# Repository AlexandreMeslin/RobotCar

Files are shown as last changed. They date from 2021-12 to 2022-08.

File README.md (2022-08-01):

# RobotCar

Lista de material:

- 1 Arduino Uno
- 1 Sensor shield v5.0
- 1 chassis duplo de acrílico para carro com 4 rodas
- 4 motores DC
- 4 rodas
- 1 módulo bluetooth HC-06 (HC-06 bluetooth module)
- 1 ponte dupla H SparkFun L298 (Dual H-Bridge motor drivers L298)
- 1 servo-motor SG90 (SG90 Micro-servo motor)
- 1 sensor de ultrassom (Ultrasonic Sensor HC-SR04)
- 1 placa de sensores versão 5 (Sensor Shield v5)
- 1 alojamento para baterias ou pilhas (3 baterias 18650 ou 4 pilhas alcalinas)

Opcionais:

- 1 Auto-falante piezo-elétrico (piezo speaker ou buzzer)
- 2 LEDs brancos 10 mm
- 2 LEDs vermelhos 5 mm
- 4 resistores 220 ohms

## Errata

Na conexão do motor: o pino 6 deve ser ligado ao ENA e o pino 13 ao IN4. Ambos, ENA e ENB devem ser ligados a saídas PWM.

## Montagem

### Montagem dos motores

Solde os fios vermelhos e pretos nos quatro motores, criando quatro conjuntos iguais. Não existe problema de polaridade, uma vez que o carro irá andar para frente e para trás, ou seja, durante o funcionamento, haverá inversão natural de tensão. Apenas certifique-se de que todos os motores foram montados igualmente.

Use um par de presilhas em cada motor para fixar o motor na parte de cima da placa do chassis inferior. As cabeças dos parafusos devem ficar voltadas para o lado de fora do carro enquanto que as porcas, para o lado de dentro.

Fixe as rodas. Os discos pretos vazados não serão utilizados nesse projeto.

Fixe as rodas com cuidado para não quebrar o acrílico. Certifique-se que as rodas estejam firmemente colocadas.

Uma boa referência para esse montagem está nesse [blog](https://create.arduino.cc/projecthub/andriy-baranov/smartphone-controlled-arduino-4wd-robot-car-14d239).

### Montagem do chassis

O servo-motor vai ser utilizado para direcionar o sensor ultrassom quando o carro andar para frente ou fizer alguma curva da mesma forma que os faróis dos carros topo de linha trabalham. Posicione o servo-motor abaixo do chassis de cima, dentro do furo maior, no lado que você considerar a frente do carro (qualquer ponta pode ser a frente). Marque e fure (dois furos) usando uma broca de aço rápido. Fixe o motor, fixe uma das barras brancas no eixo do servo. Marque e fure (dois furos) o acrílico em L. Fixe usando um parafuso para plástico bem fino. Fixe o sensor ultrassom usando cola quente no acrílico em L.

Posicione o Arduino logo após o sensor em L, depois a ponte, com o discipador de calor voltado para frente, e, na parte mais distante do sensor ultrassom, o alojamento das baterias. Note que dificilmente algum furo vai poder ser aproveitado. Faça as marcações e novos furos para fixar os três elementos. Fixe os três elementos.

Fixe os seis espaçadores separando as duas camadas do chassis.

Após essa etapa, as partes mecânicas devem estar prontas, faltando o cabeamento e o software.

### Cabeamento

Coloque o sensor shield sobre o Arduino.

#### **Cabeamento do sensor ultrassom:**

Alimentação:

- +5V
- GND

I/O:

- GPIO8: TRIGPIN
- GPIO9: ECHOPIN

Para fixar o sensor no suporte acrílico em L foi necessário fazer 4 furos com brocas de 1 mm. Para encaixar o cristal foi necessário limar um pouco o acrílico porque eu utilizei parafusos de óculos e eles eram curtos.

Usando um cabo de quatro fios, conecte o sensor no shield como mostrado a seguir:

| Sensor Ultrassom | Sensor Shield |
| --- | --- |
| Echo | 9 |
| Trig | 8 |
| Vcc | V |
| Gnd | G |

#### **Cabeamento do servo-motor**

Alimentação:

- +5V
- GND

I/O:

- GPIO7: SERVOPIN

O servo-motor é usado para posicionar o sensor ultrassônico sempre na direçao do movimento do carro.

O acrílico deve ser aparafusado em cima do motor usando a barra reta que vem com o motor.

| Servo Motor | Sensor Shield |
| --- | --- |
|  Control  | 7 |
| Vcc | V |
| Gnd | G |

#### **Cabeamento do módulo Bluetooth:**

Alimentação:

- +5V
- GND

I/O:

- TX: TxD
- RX: RxD

Prenda com uma gravatinha (ou um lacre de embalagem de pão) o módulo Bluetooth. Note que ele não tem furação de fixação. Com um cabo de quatro fios, conecte o módulo no shield como mostrado a seguir:

| Módulo Bluetooth | Sensor Shield |
| --- | --- |
| RXD | TX |
| TXD | RX |
| VCC | V |
| GND | G |

#### **Cabeamento da ponte:**

:warning: Ver ERRATA!

Conecte os dois fios vermelhos dos motores direito em OUT4.

Conecte os dois fios pretos dos motores direito em OUT3.

Conecte os dois fios vermelhos dos motores esquerdo em OUT2.

Conecte os dois fios pretos dos motores esquerdo em OUT1.

Termine o cabeamento da ponte como mostrado a seguir (antes, retire os dois jumpers que estão na ponte para fazer o cabeamento):

| Módulo Ponte | Sensor Shield |
| - | - |
| ENA | 5 |
| IN1 | 2 |
| IN2 | 3 |
| IN3 | 4 |
| IN4 | 13 |
| ENB | 6 |

#### **Cabeamento da energia:**

Conecte o fio vermelho da bateria em +12V da ponte.

Conecte o fio preto da bateria em GND da ponte. Nesse mesmo ponto, conecte um fio preto até GND do sensor shield.

Conecte o fio vermelho de VCC da ponte até VCC do shield.

Opcionalmente, conecte o positivo (vermelho) do suporte da bateria no módulo de potência através de uma chave liga-desliga.

#### **Opcionais:**

- LEDs brancos na frente. Dois LEDs brancos, cada um com um resistor de 220 Ω ligados no pino 10
- LEDS vermelhos atrás. Dois LEDs vermelhos, cada um com um resistor de 220 Ω ligados no pino 1
- Buzina: Uma buzina (buzzer) ligada no pino 11
- Chave liga/desliga em série com as baterias.

### Código

:warning: IMPORTANTE: antes de fazer upload do código, não se esqueça de desconectar os pinos TX e RX do shield. Eles estão conectados ao Bluetooth, que usa os mesmos pinos da interface serial USB. Lembre-se de reconectar para poder usar o carro.

## Histórico

- 2022-08-01: Inclusão da câmera frontal no carro.
- 2022-02-17b: Criação de um README (quase) descente.
- 2002-02-17: Primeira versão com controle de versão.

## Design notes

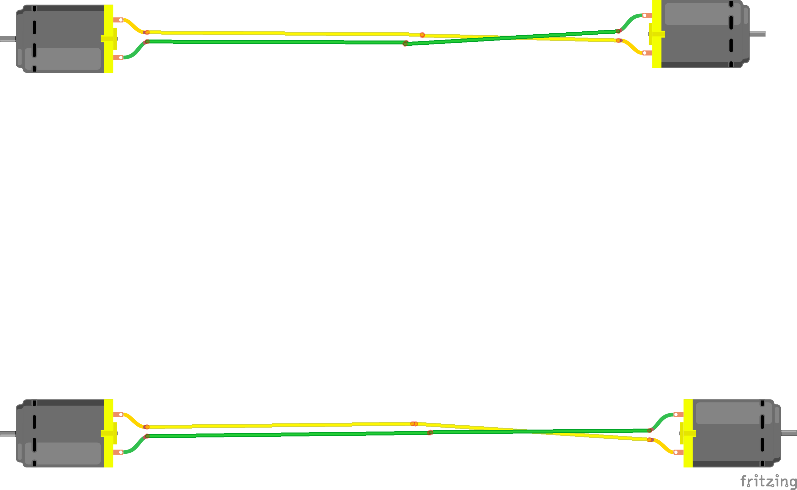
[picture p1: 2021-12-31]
CarroRobo_motores.png

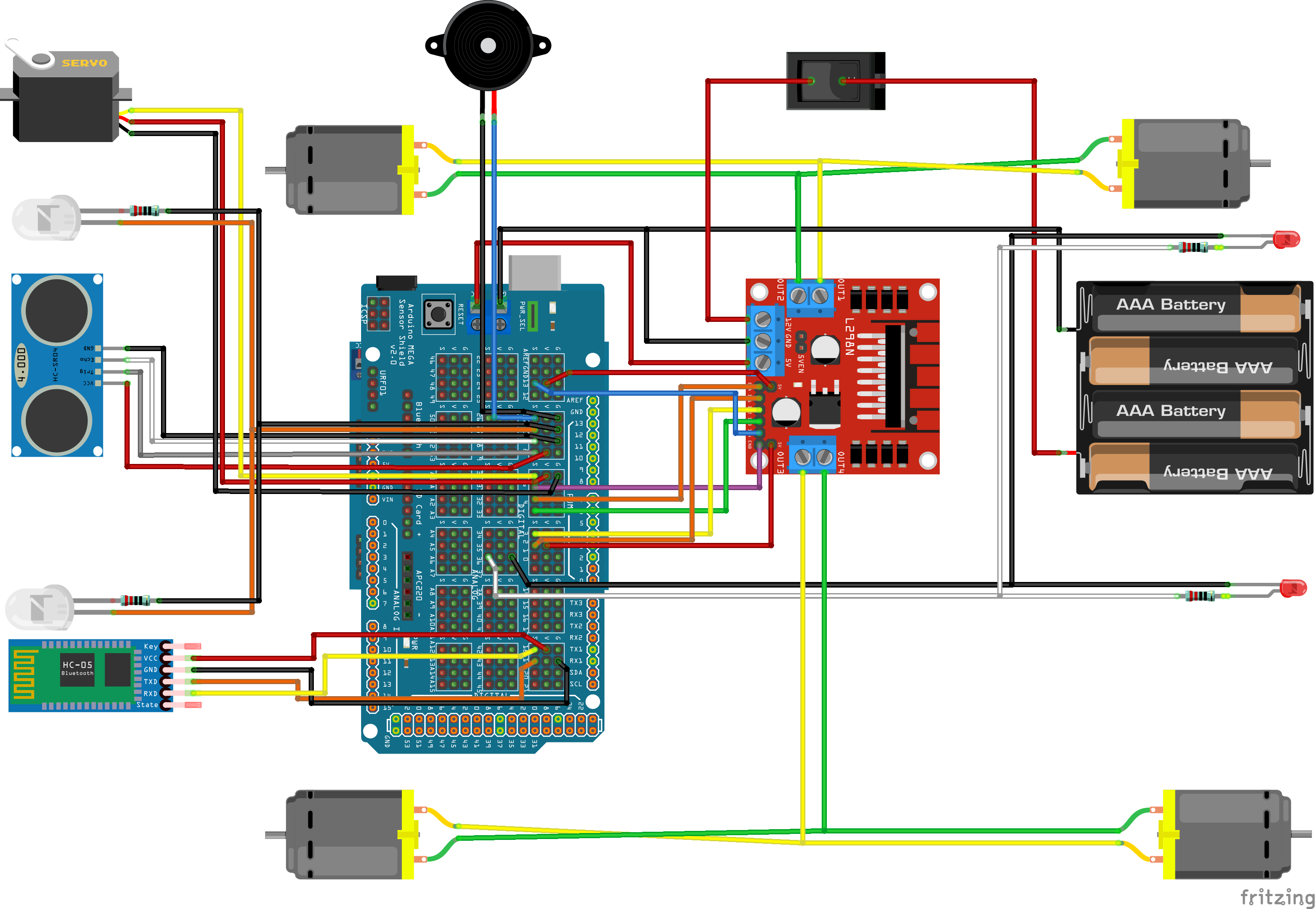
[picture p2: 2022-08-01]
CarroRoboMega_bb.png

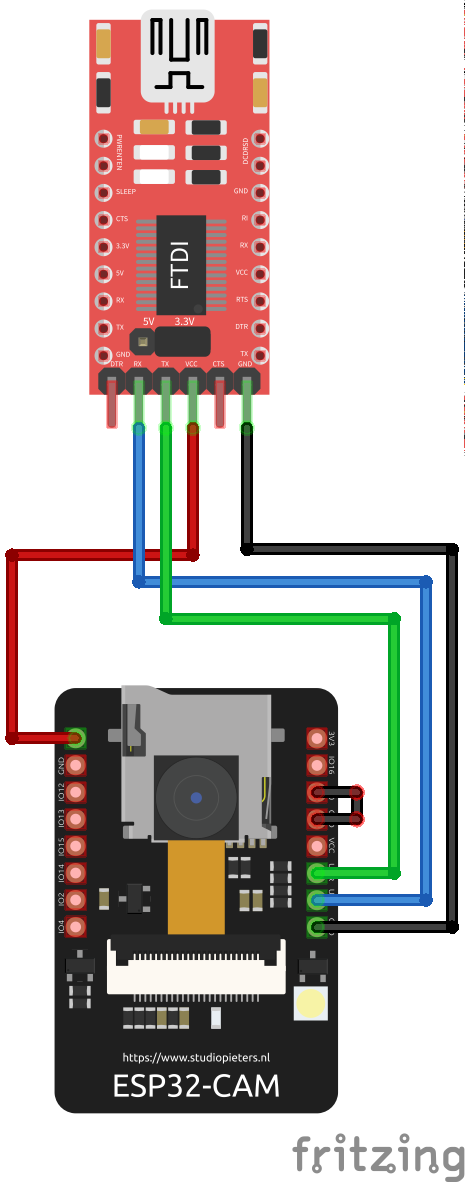
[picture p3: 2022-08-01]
GravacaoESP32Cam_bb.png

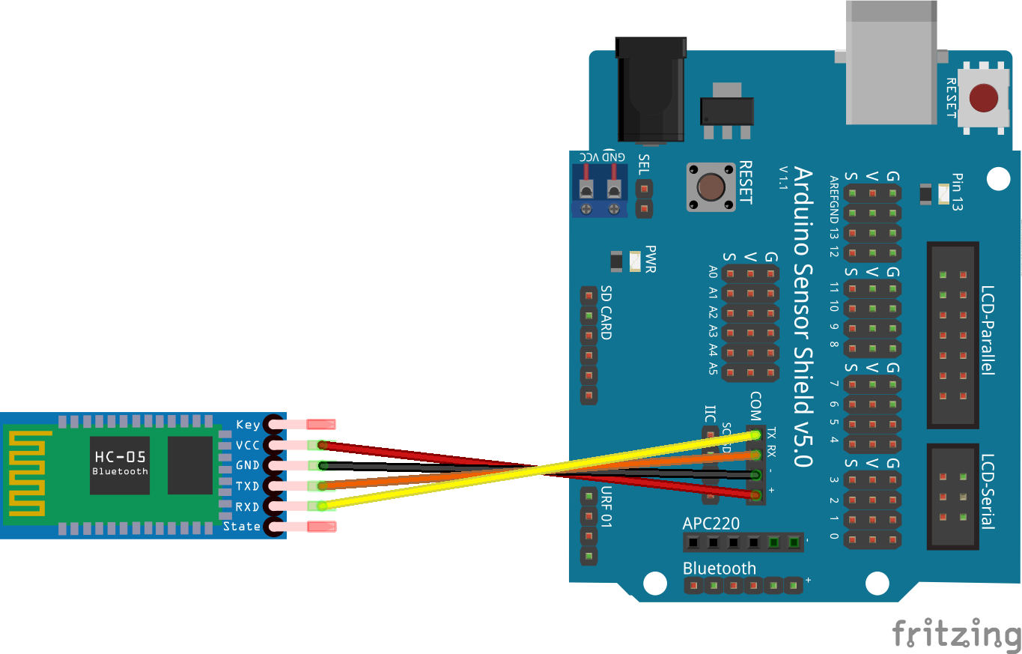
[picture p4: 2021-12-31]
CarroRobo_bluetooth.png

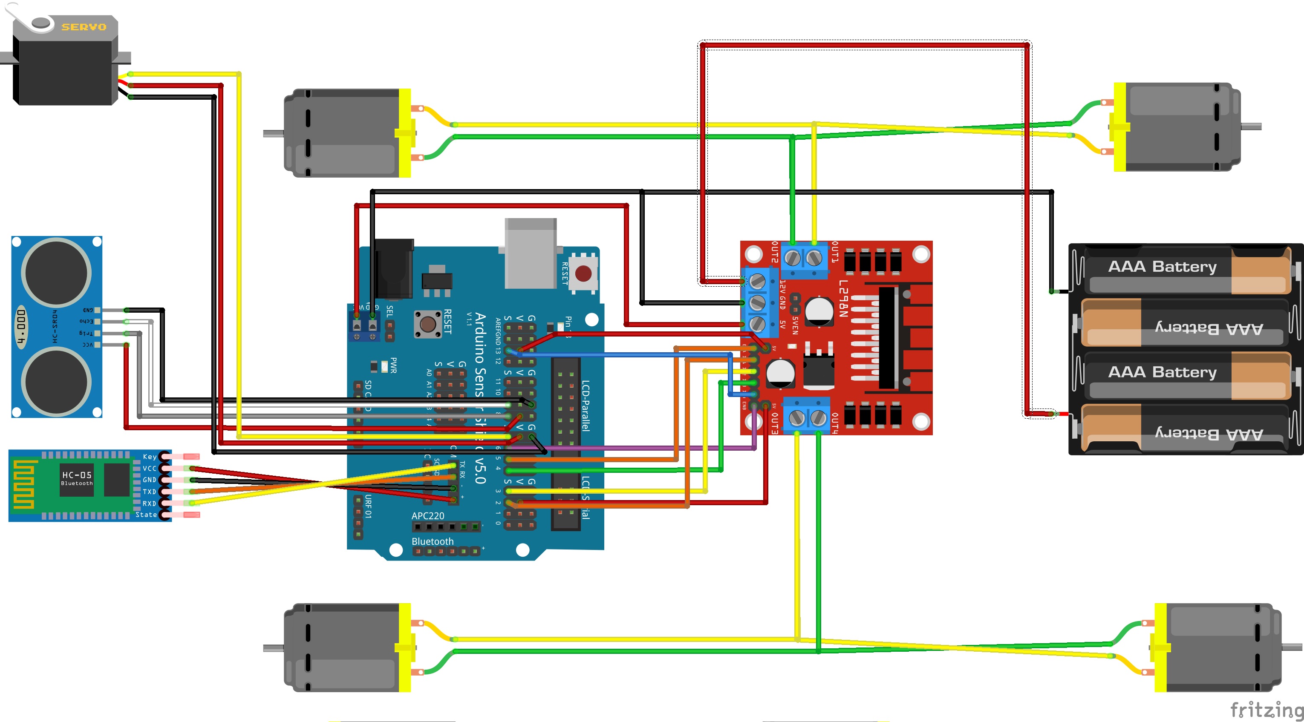
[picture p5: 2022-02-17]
CarroRobo_basico.png

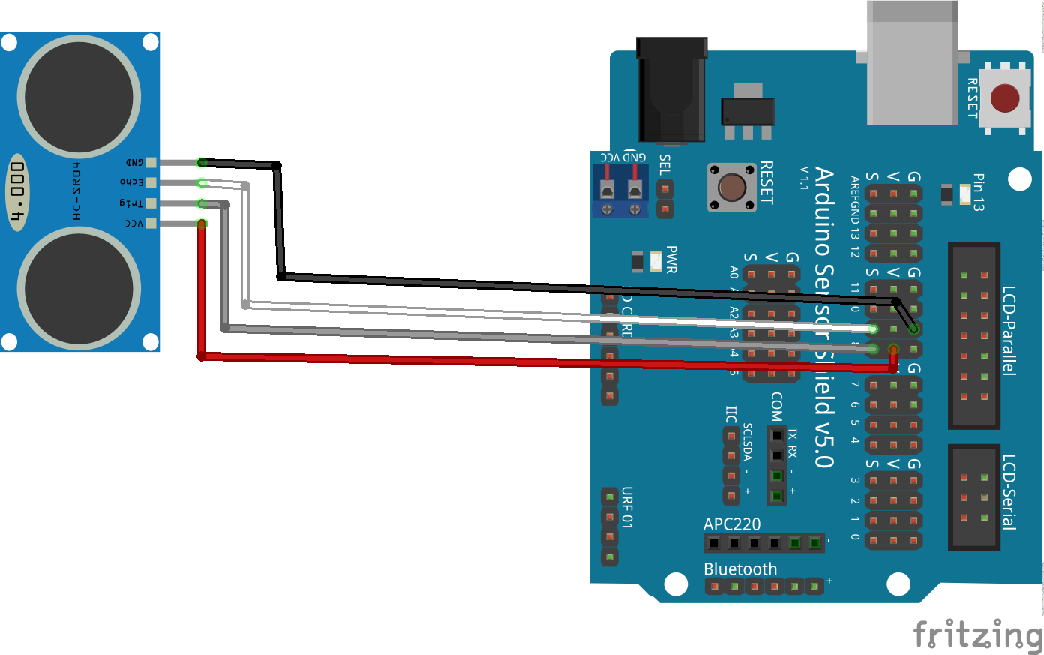
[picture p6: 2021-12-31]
CarroRobo_ultrasom.png

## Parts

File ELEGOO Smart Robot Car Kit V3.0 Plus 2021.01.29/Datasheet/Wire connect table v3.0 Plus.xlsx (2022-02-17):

wire connect table
Arduino UNO | IO shield | Module
D10 | S10 |  | Line tracking module #1
D4 | S4 |  | Line tracking module #2
D2 | S2 |  | Line tracking module #3
 | G |  | SG90
 | V
D3 | S3
D5 | S5 | ENA | L298N(Motor driver board)
D6 | S6 | ENB
D7 | S7 | N1
D8 | S8 | N2
D9 | S9 | N3
D11 | S11 | N4
 | G |  | Infrared receicer module
 | V
D12 | S12
 | V | Vcc | Ultrasonic Sensor module
A5 | A5 | Trlg
A4 | A4 | Echo
 | G | Gnd
 | + | VCC | Bluetooth module
 | - | GND
D0(RX) | RX | TXD
D1(TX) | TX | RXD
L298N board | Motor |  | Control Pin
OUT1 | Brack wire | Right back motor | N3,N4
 | Red wire
OUT2 | Brack wire | Right front motor
 | Red wire
OUT3 | Brack wire | Left front motor | N1,N2
 | Red wire
OUT4 | Brack wire | Left back motor
 | Red wire

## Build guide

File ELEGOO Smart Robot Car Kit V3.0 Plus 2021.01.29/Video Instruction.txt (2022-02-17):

To watch video tutorial please refer to below links:

Elegoo Robot Car Kit V3.0 Plus Assembly Tutorial: 
https://youtu.be/vVwwaEWZEls

Elegoo Robot Car Kit V3.0 Plus Functions Demonstration: 
https://youtu.be/HbJaBnU3jC0

Should you have any questions during usage please feel free to let us know.

service@elegoo.com

Elegoo Team

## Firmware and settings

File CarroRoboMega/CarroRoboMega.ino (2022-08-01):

/*
*/

#include <Servo.h>
#include <NewPing.h>

void forward(void);
void back(void);
void left(void);
void right(void);
void stopAll(void);
int readPing(void);
void forwardRight(void);
void forwardLeft(void);

/*
 * Ultrasonic sensor
 */
#define TRIGPIN 8
#define ECHOPIN 9
const int maximumDistance = 100;
NewPing sonar(TRIGPIN, ECHOPIN, maximumDistance); //sensor function
int distance;
unsigned long previousMillis = 0;        // will store last time distance was updated
 
/*
 * Motor
 * Board              Pins                  Frequency
 * Uno, Nano, Mini    3, 5, 6, 9, 10, 11    490 Hz (pins 5 and 6: 980 Hz)
 * Mega               2 - 13, 44 - 46       490 Hz (pins 4 and 13: 980 Hz)
 */
unsigned char carSpeed = 0x70;  // 60-80
boolean movingForward = false;
// Left Motor
const int motorEnLeft = 6;
const int motorInLeft1 = 41;
const int motorInLeft2 = 42;
// Right Motor
const int motorEnRight = 5;
const int motorInRight3 = 39;
const int motorInRight4 = 40;

/*
 * Servo
 */
int servoPin = 7; // Declare the Servo pin 
Servo servo;      // Create a front servo object 

/*
 * Lights
 */
const int ledPinFrontRight = 10;  // the number of the LED pin
const int ledPinFrontLeft  = 10;
const int ledPinRearRight  = 12;  // the number of the LED pin
const int ledPinRearLeft   = 12;  // the number of the LED pin

/*
 * Horn
 */
const int hornPin = 11;

// Generally, you should use "unsigned long" for variables that hold time
// The value will quickly become too large for an int to store

void setup() {
  // Serial setup
  Serial.begin(9600);
  Serial1.begin(9600);
  
  // Motor setup
  pinMode(motorInLeft1, OUTPUT);
  pinMode(motorInLeft2, OUTPUT);
  pinMode(motorInRight3, OUTPUT);
  pinMode(motorInRight4, OUTPUT);

//  pinMode(motorEnLeft, OUTPUT); 
//  pinMode(motorEnRight, OUTPUT); 

  // Servo setup
  servo.attach(servoPin); 

  // Light setup
  // set the digital pin as output:
  pinMode(ledPinFrontRight, OUTPUT);
  pinMode(ledPinFrontLeft, OUTPUT);
  pinMode(ledPinRearRight, OUTPUT);
  pinMode(ledPinRearLeft, OUTPUT);
  digitalWrite(ledPinFrontRight, LOW);
  digitalWrite(ledPinFrontLeft, LOW);
  digitalWrite(ledPinRearRight, LOW);
  digitalWrite(ledPinRearLeft, LOW);

  /*
   * Ultrasonic
   */
  pinMode(TRIGPIN, OUTPUT);
  pinMode(ECHOPIN, INPUT);
  delay(2000);
  distance = readPing();
  delay(100);
  distance = readPing();
  delay(100);
  distance = readPing();
  delay(100);
  distance = readPing();
  delay(100);
  
  Serial.println("Começando...\n");
}

void loop() {
  static char command;

  if(distance < 20) {
      digitalWrite(ledPinFrontRight, HIGH);
      digitalWrite(ledPinFrontLeft, HIGH);
      digitalWrite(ledPinRearRight, HIGH);
      digitalWrite(ledPinRearLeft, HIGH);
      Serial.println("Aqui 2");
      if(movingForward) stopAll();
  }

  command = Serial1.read();
  switch(command) {
    case 'b':
    case 'B': // move back
      servo.write(90);
      back();
      break;
    case 'D': // Stop all
      Serial.println("Aqui 3");
      stopAll();
      break;
    case 'f':
    case 'F': // move forward
      servo.write(90);
      forward();
      break;
    case 'G': // Move forward left
      servo.write(90+45);
      forwardLeft();
      break;
    case 'H': // Move back left
      servo.write(90);
      backLeft();
      break;
    case 'I': // Move forward right
      servo.write(90-45);
      forwardRight();
      break;
    case 'J': // Move back right
      servo.write(90);
      backRight();
      break;
    case 'L': // move left
      servo.write(180);
      left();
      break;
    case 'R': // Right
      servo.write(0);
      right();
      break;
    case 'S': // Stop
      Serial.println("Aqui 4");
      stopAll();
      break;
    case 'V': // horn on
      analogWrite(hornPin, 127);  // 50% duty cicle
      break;
    case 'v': // horn off
      digitalWrite(hornPin, 0);   // 0% duty cicle
      break;
    case 'W': // Front lights on
      digitalWrite(ledPinFrontRight, HIGH);
      digitalWrite(ledPinFrontLeft, HIGH);
      break;
    case 'w': // Front lights off
      digitalWrite(ledPinFrontRight, LOW);
      digitalWrite(ledPinFrontLeft, LOW);
      break;
    case 'U': // back lights on
      digitalWrite(ledPinRearRight, HIGH);
      digitalWrite(ledPinRearLeft, HIGH);
      break;
    case 'u': // back ligths off
      digitalWrite(ledPinRearRight, LOW);
      digitalWrite(ledPinRearLeft, LOW);
      break;
    case '0': // Speed 0;
      carSpeed = 255*0/100;
      break;
    case '1': // Speed 10;
      carSpeed = 255*10/100;
      break;
    case '2': // Speed 20;
      carSpeed = 255*20/100;
      break;
    case '3': // Speed 30;
      carSpeed = 255*30/100;
      break;
    case '4': // Speed 40;
      carSpeed = 255*40/100;
      break;
    case '5': // Speed 50;
      carSpeed = 255*50/100;
      break;
    case '6': // Speed 60;
      carSpeed = 255*60/100;
      break;
    case '7': // Speed 70;
      carSpeed = 255*70/100;
      break;
    case '8': // Speed 80;
      carSpeed = 255*80/100;
      break;
    case '9': // Speed 90;
      carSpeed = 255*90/100;
      break;
    case 'q': // Speed 100;
      carSpeed = 255*100/100;
      break;
  }
  distance = readPing();
}

/**
 * Motor forward
 */
void forward(void){
  movingForward = true;
  if(distance < 20) {
    Serial.println("Aqui 1");
    stopAll();
  } else {
    digitalWrite(motorInLeft1,HIGH);
    digitalWrite(motorInLeft2,LOW);
    digitalWrite(motorInRight3,LOW);
    digitalWrite(motorInRight4,HIGH);
    analogWrite(motorEnLeft,carSpeed);
    analogWrite(motorEnRight,carSpeed);
  }
//  Serial.print("Forward: "); Serial.println(carSpeed, HEX);
}

void forwardRight(){
  movingForward = true;
  if(distance < 20) {
    stopAll();
  } else {
    digitalWrite(motorInLeft1, HIGH);
    digitalWrite(motorInLeft2, LOW);
    digitalWrite(motorInRight3, LOW);
    digitalWrite(motorInRight4, HIGH);
    analogWrite(motorEnLeft, carSpeed);
    analogWrite(motorEnRight, LOW);
  }
//  Serial.print("Forward right: ");   Serial.print(speedLeft, HEX);  Serial.println(speedRight, HEX);
}

void forwardLeft(void){
    movingForward = true;
  if(distance < 20) {
    stopAll();
  } else {
    digitalWrite(motorInLeft1, HIGH);
    digitalWrite(motorInLeft2, LOW);
    digitalWrite(motorInRight3, LOW);
    digitalWrite(motorInRight4, HIGH);
    analogWrite(motorEnLeft,LOW);
    analogWrite(motorEnRight, carSpeed);
  }
//  Serial.println("Forward left");
}
 
void back(){
  movingForward = false;
  digitalWrite(motorInLeft1,LOW);
  digitalWrite(motorInLeft2,HIGH);
  digitalWrite(motorInRight3,HIGH);
  digitalWrite(motorInRight4,LOW);
  analogWrite(motorEnLeft,carSpeed);
  analogWrite(motorEnRight,carSpeed);
//  Serial.print("Back: "); Serial.println(carSpeed, HEX);
//  Serial.println(distance, DEC);
}
 
void backRight(void){
  movingForward = false;
  digitalWrite(motorInLeft1, LOW);
  digitalWrite(motorInLeft2, HIGH);
  digitalWrite(motorInRight3, HIGH);
  digitalWrite(motorInRight4, LOW);
  analogWrite(motorEnLeft, carSpeed);
  analogWrite(motorEnRight, LOW);
//  Serial.println("Back right");
}
 
void backLeft(void){
  movingForward = false;
  digitalWrite(motorInLeft1,LOW);
  digitalWrite(motorInLeft2,HIGH);
  digitalWrite(motorInRight3,HIGH);
  digitalWrite(motorInRight4,LOW);
  analogWrite(motorEnLeft, LOW);
  analogWrite(motorEnRight,carSpeed);
//  Serial.println("Back left");
}
 
void right(){
  digitalWrite(motorInLeft1, HIGH);
  digitalWrite(motorInLeft2, LOW);
  digitalWrite(motorInRight3, HIGH);
  digitalWrite(motorInRight4, LOW);
  analogWrite(motorEnLeft, carSpeed);
  analogWrite(motorEnRight, carSpeed);
//  Serial.println("Right");
}
 
void left(){
  digitalWrite(motorInLeft1, LOW);
  digitalWrite(motorInLeft2, HIGH);
  digitalWrite(motorInRight3, LOW);
  digitalWrite(motorInRight4, HIGH); 
  analogWrite(motorEnLeft, carSpeed);
  analogWrite(motorEnRight, carSpeed);
//  Serial.println("Left");
}
 
void stopAll(){
  movingForward = false;
  analogWrite(motorEnRight,LOW);
  analogWrite(motorEnLeft,LOW);
  digitalWrite(ledPinRearRight, HIGH);
  digitalWrite(ledPinRearLeft, HIGH);
//  Serial.println("Stop!");
}

/**
 * Ultrasonic sensor reader
 */
int readPing(){
  static unsigned long currentMillis;
  static unsigned long deltaT;

  currentMillis = millis();
  deltaT = currentMillis - previousMillis;
  previousMillis = currentMillis;
  if(deltaT < 70) delay(70 - deltaT);
//  delay(70);
  int cm = sonar.ping_cm();
  if (cm==0){
    cm=250;
  }
  return cm;
}

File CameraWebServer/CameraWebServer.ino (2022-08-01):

/*
 * From https://randomnerdtutorials.com/esp32-cam-video-streaming-web-server-camera-home-assistant/
 * 
 * Not using OTA ==> use with board AI Thinker ESP32-CAM
 * 
 * Using OTA:
 * (From https://www.esp32.com/viewtopic.php?t=14700#p65758)
 * - Use ESP32 dev module instead of AI Thinker ESP32-Cam
 * - Configure Partition Scheme to default 4MB with spiffs
 * - Enable PSRAM
 * and it works using this (not sure if it is necessary):
 * - Upload Speed: 921600
 * - CPU Frequency: 240MHz (WiFi/BT)
 * - Flash Frequency: 80MHz
 * - Flash Mode: QIO
 * - Flash Size: 4MB (32Mb)
 * - Core Debug Level: None
 * 
 * OTA only works during boot (40 seconds) to not increase the delay in the stream
 * 
 * URL: http://<ip address>:80
 * URL: http://<ip address>:81/stream
 */
 
#define DEBUG_____

/*
 * GPIO assignment
 * 0  - XCLK
 * 1
 * 2
 * 3
 * 4  - LED_FLASH
 * 5  - Y2
 * 6
 * 7
 * 8
 * 9
 * 10
 * 11
 * 12
 * 13
 * 14
 * 15
 * 16
 * 17
 * 18 - Y3
 * 19 - Y4
 * 20
 * 21 - Y5
 * 22 - PCKL
 * 23 - HREF
 * 24
 * 25 - VSYNC
 * 26 - SIOD
 * 27 - SIOC
 * 28
 * 29
 * 30
 * 31
 * 32 - PWDN
 * 33 - LED
 * 34 - Y8
 * 35 - Y9
 * 36 - Y6
 * 37
 * 38
 * 39 - Y7
 */

#include <Arduino.h>
#include <ArduinoOTA.h>
// 1 #include <BluetoothSerial.h>
#include <esp_camera.h>
#include <esp_http_server.h>
#include <esp_timer.h>
#include <ESPmDNS.h>
#include <fb_gfx.h>
#include <img_converters.h>
#include <soc/soc.h>            // disable brownout problems
#include <soc/rtc_cntl_reg.h>   // disable brownout problems
#include <WiFi.h>
#include <WiFiUdp.h>
#include <credentials.h>        // My WiFi credentials

const char *ssid = MY_SSID;
const char *password = MY_PASSWORD;
#define OTA_HOSTNAME  "CameraWideOTA"

/*
 * Camera
 */
#define PART_BOUNDARY "123456789000000000000987654321"

#define PWDN_GPIO_NUM     32
#define RESET_GPIO_NUM    -1
#define XCLK_GPIO_NUM      0
#define SIOD_GPIO_NUM     26
#define SIOC_GPIO_NUM     27
  
#define Y9_GPIO_NUM       35
#define Y8_GPIO_NUM       34
#define Y7_GPIO_NUM       39
#define Y6_GPIO_NUM       36
#define Y5_GPIO_NUM       21
#define Y4_GPIO_NUM       19
#define Y3_GPIO_NUM       18
#define Y2_GPIO_NUM        5
#define VSYNC_GPIO_NUM    25
#define HREF_GPIO_NUM     23
#define PCLK_GPIO_NUM     22

/*
 * LED
 */
#define LED_PIN 33
/*
 * Macros
 */

#ifdef DEBUG_____
#define myprint(x)    {Serial.print(x);   client.print(x);}
#define myprintln(x)  {Serial.println(x); client.println(x);}
#else
#define myprint(x)    {client.print(x);}
#define myprintln(x)  {client.println(x);}
#endif

#ifdef NCE
#define HOST "10.10.15.222"
#define PORT (8752)
#else
#define HOST "10.0.0.101"
#define PORT (8752)
#endif

static const char* _STREAM_CONTENT_TYPE = "multipart/x-mixed-replace;boundary=" PART_BOUNDARY;
static const char* _STREAM_BOUNDARY = "\r\n--" PART_BOUNDARY "\r\n";
static const char* _STREAM_PART = "Content-Type: image/jpeg\r\nContent-Length: %u\r\n\r\n";

httpd_handle_t camera_httpd = NULL;
httpd_handle_t stream_httpd = NULL;

static const char PROGMEM INDEX_HTML[] = R"rawliteral(
<html>
  <head>
    <title>ESP32-CAM Robot</title>
    <meta name="viewport" content="width=device-width, initial-scale=1">
  </head>
  <body>
    <center>
      <img src="" id="photo" style="width: auto; max-width: 100%; height: auto;">
    </center>
    <script>
      document.getElementById("photo").src = window.location.href.slice(0, -1) + ":81/stream";
    </script>
  </body>
</html>
)rawliteral";

/*
 * New types
 */
typedef unsigned long MY_TIME_T;

/*
 * Prototypes
 */
void myDelay(MY_TIME_T waitTime);

/*
 * To enable Bluetooth serial monitor (from Bluetooth example)
 */
// 1 BluetoothSerial SerialBT;


// WiFi console
WiFiClient client;

void setup() {
  WRITE_PERI_REG(RTC_CNTL_BROWN_OUT_REG, 0); //disable brownout detector
  
  Serial.begin(115200);
  Serial.setDebugOutput(false);

// 1  SerialBT.begin("RobotCar"); //Bluetooth device name
  
  // Wi-Fi connection
/* 1
  WiFi.mode(WIFI_STA);
  Serial.printf("Usando SSDI %s and password %s\n", ssid, password);
  WiFi.begin(ssid, password);
  while(WiFi.waitForConnectResult() != WL_CONNECTED) {
    myprintln("Connection Failed! Try a new SSID/Password via Bluetooth.");
    String ssid = readSSID();
    String password = readPassword();
    myprint("Trying with "); myprint(ssid.c_str()); myprint(" and "); myprintln(password.c_str()); 
    SerialBT.print("Trying with "); SerialBT.print(ssid.c_str()); SerialBT.print(" and "); SerialBT.println(password.c_str()); 
    WiFi.mode(WIFI_STA);
    WiFi.begin(ssid.c_str(), password.c_str());
    delay(5000);
//    myprintln("Connection Failed! Rebooting...");
//    ESP.restart();
  }
  myprintln("\nWiFi connected");
*/

  // Connect to Wi-Fi network
  WiFi.mode(WIFI_STA);
#ifdef NCE
  WiFi.begin(ssid);
#else
  WiFi.begin(ssid, password);
#endif
  while (WiFi.waitForConnectResult() != WL_CONNECTED) {
    Serial.printf("Connection Failed! Rebooting...");
    delay(10000);
    ESP.restart();
  }
  myprintln("Connected to WiFi");

  // Arduino OTA
  ArduinoOTA.setHostname(OTA_HOSTNAME);

  // No authentication by default
  // ArduinoOTA.setPassword("admin");

  // Password can be set with it's md5 value as well
  // MD5(admin) = 21232f297a57a5a743894a0e4a801fc3
  // ArduinoOTA.setPasswordHash("21232f297a57a5a743894a0e4a801fc3");

  ArduinoOTA.onStart([]() {
      String type;
      if (ArduinoOTA.getCommand() == U_FLASH) {
        type = "sketch";
      } else { // U_SPIFFS
        type = "filesystem";
      }

      // NOTE: if updating SPIFFS this would be the place to unmount SPIFFS using SPIFFS.end()
      myprintln("Start updating " + type);
    });
    ArduinoOTA.onEnd([]() {
      Serial.println("\nEnd");
    });
    ArduinoOTA.onProgress([](unsigned int progress, unsigned int total) {
      Serial.printf("Progress: %u%%\r", (progress / (total / 100)));
    });
    ArduinoOTA.onError([](ota_error_t error) {
    printf("Error[%u]: ", error);
    if (error == OTA_AUTH_ERROR) {
      myprintln("Auth Failed");
    } else if (error == OTA_BEGIN_ERROR) {
      myprintln("Begin Failed");
    } else if (error == OTA_CONNECT_ERROR) {
      myprintln("Connect Failed");
    } else if (error == OTA_RECEIVE_ERROR) {
      myprintln("Receive Failed");
    } else if (error == OTA_END_ERROR) {
      myprintln("End Failed");
    }
  });
  ArduinoOTA.begin();
  myprintln("Ready!");

  // WiFi console
  if(!client.connect(HOST, PORT)) {
    myprint("Could not connect to WiFi console at ");
  } else {
    myprint("Connected to WiFi console at ");  
  }
  myprint(HOST);
  myprint(":");
  myprintln(PORT);
  delay(1000);
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

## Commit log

2021-12-31 full first commit
    [CarroRobo.fzz]
2022-08-01 Camera v1
    [CarroRobo.fzz, CarroRoboMega.fzz, Copy of CarroRoboMega.fzz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]
